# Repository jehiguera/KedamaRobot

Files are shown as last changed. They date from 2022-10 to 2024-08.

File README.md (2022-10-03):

# KedamaRobot
Autonomous Robot Kedama based on TM4C123G microcontroller

# The real Kedama cat


In this project, I have implemented a digital twin of my cat Kedama. The autonomous robot is based on a TM4C123G microcontroller namely TIVA C series TM4C123G by Texas instrumentals. 
The document [Autonomous Mobile robot Kedama.pdf] explains a detailed introduction of the architecture, requirements and firmware modules implemented using the IDE Keil MDK-ARM Plus version 5.
The microcontroller development board used for this project is TM4C123 Tiva C Series LaunchPad. 

https://github.com/jehiguera/KedamaRobot/blob/main/Autonomous%20Mobile%20Robot%20Kedama.pdf

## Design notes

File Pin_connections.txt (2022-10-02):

#define ECHO    (1U<<6)	// PB6(INPUT)
#define TRIGGER (1U<<4) // PA4 (OUTPUT)
#define BLUE_LED 1U<<2) //PF2 onboard Blue LED
#define IR_PIN  (1U<<5) //PA5 (INPUT)
#define SERVO   (1U<<3)	// PF3 (OUTPUT)
#define MOTOR1  (1U<<2)	// PE2 (OUTPUT)
#define MOTOR2  (1U<<3)	// PE3 (OUTPUT)

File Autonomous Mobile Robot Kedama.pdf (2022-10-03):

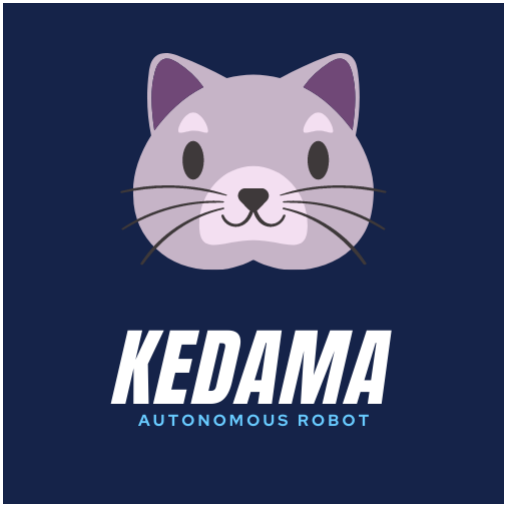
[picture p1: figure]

# Author: Jorge Higuera Portilla jhiguera@ieee.org Castelldefels, Barcelona, Spain. 15/05/2021

1

# The real Kedama cat

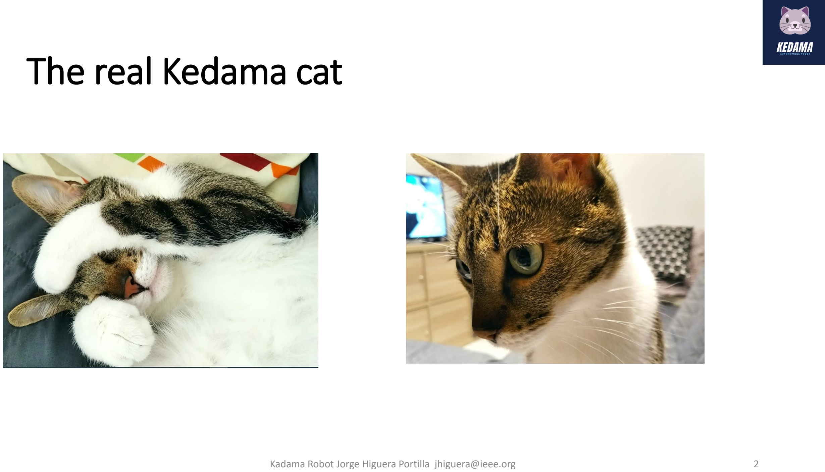
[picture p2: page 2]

Kadama Robot Jorge Higuera Portilla jhiguera@ieee.org | 2

# Kedama digital twin Robot Requirements

# Inputs and outputs

## Head: Ultrasonic sensor (Input / output)

## Intangible

## Neck: Servo Motor (output)

## Tail: IR sensor (Input)

## Limbs: DC motors (output)

## Tangible

## Timing: internal timers and HW interruptions

## Light: natural and artificial light detection

## Behavioral robot state: discovering, playing, shy

## Eco-location: ultrasonic wave

## Head: LEDs (output)

# Robot architecture

## Tail: IR sensor

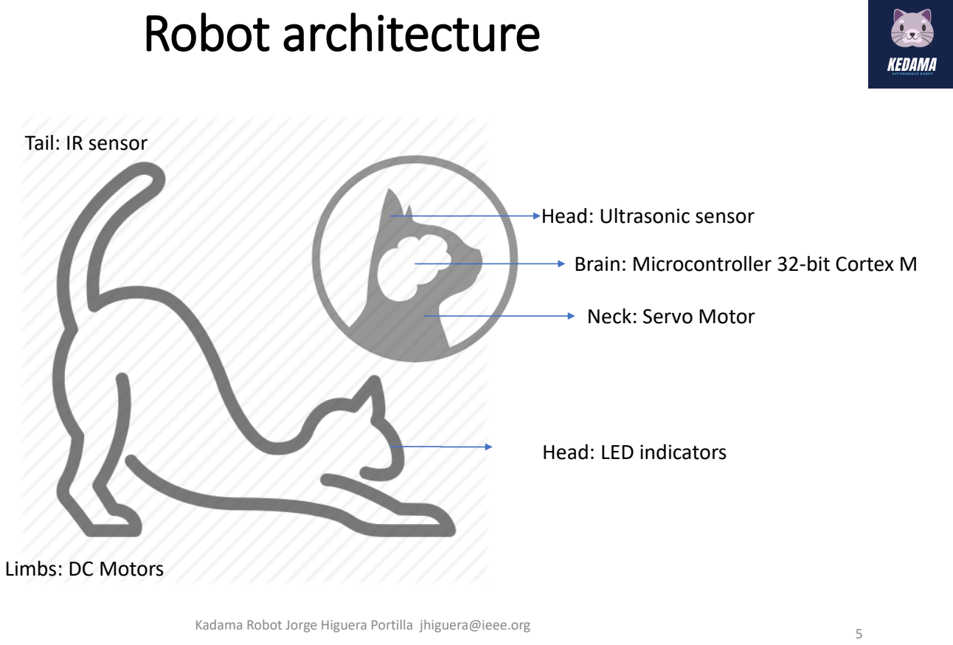
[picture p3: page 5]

## Brain: Microcontroller 32-bit Cortex M

## Head: Ultrasonic sensor

## Neck: Servo Motor

## Limbs: DC Motors

## Head: LED indicators

# Component and supplies

## (1 und) Tiva TM4C123G

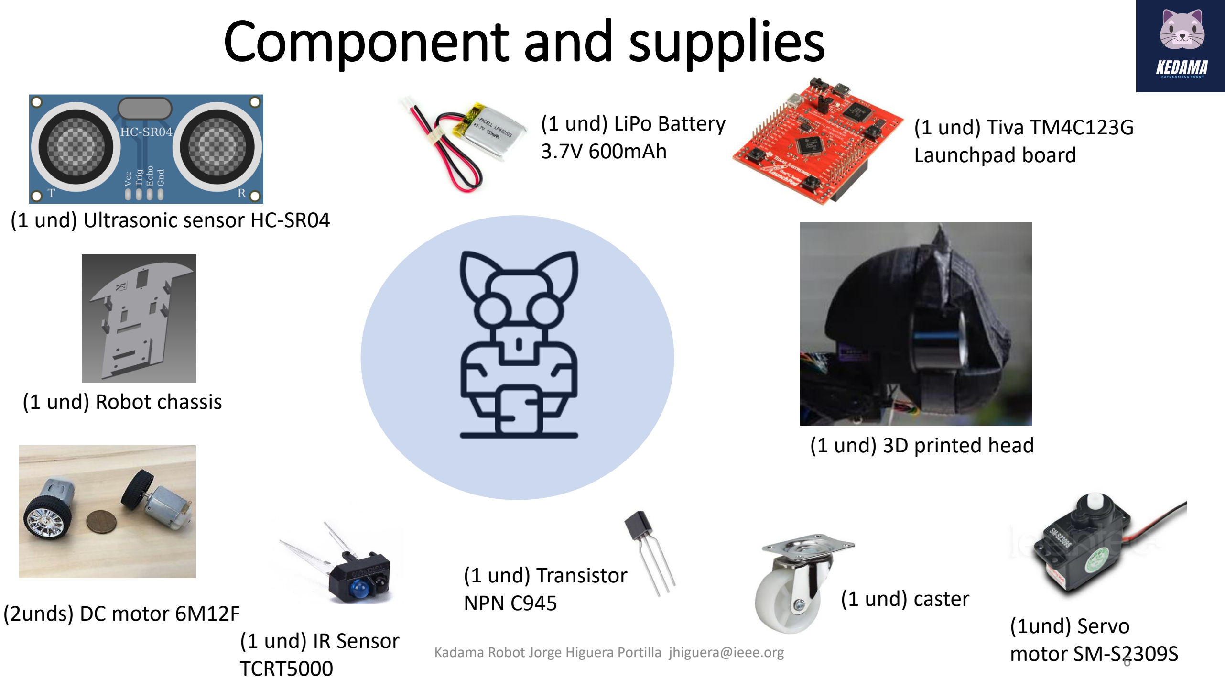
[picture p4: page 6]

## (1 und) Ultrasonic sensor HC-SR04

## Launchpad board

## (1 und) caster (2unds) DC motor 6M12F

## (1 und) 3D printed head

## (1 und) Robot chassis

## (1und) Servo motor SM-S2309S

## (1 und) Transistor NPN C945

## (1 und) IR Sensor TCRT5000

## (1 und) LiPo Battery 3.7V 600mAh

# Brain and Head configuration

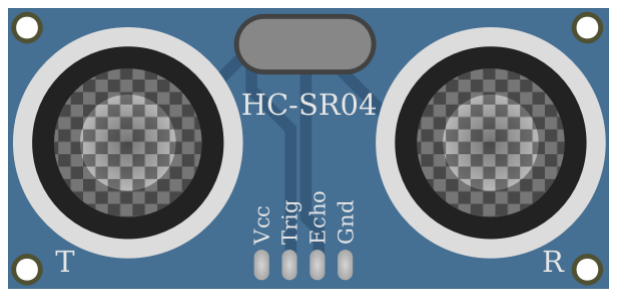
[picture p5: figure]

## Ultrasonic sensor HC-SR04

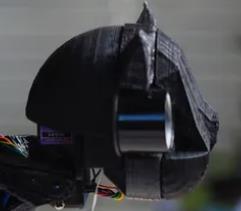
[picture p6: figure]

## 3D printed head

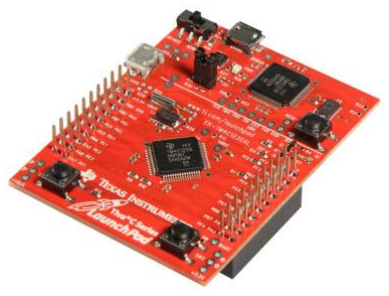
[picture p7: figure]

## Tiva TM4C123G Launchpad board with internal LEDs

# Tail configuration

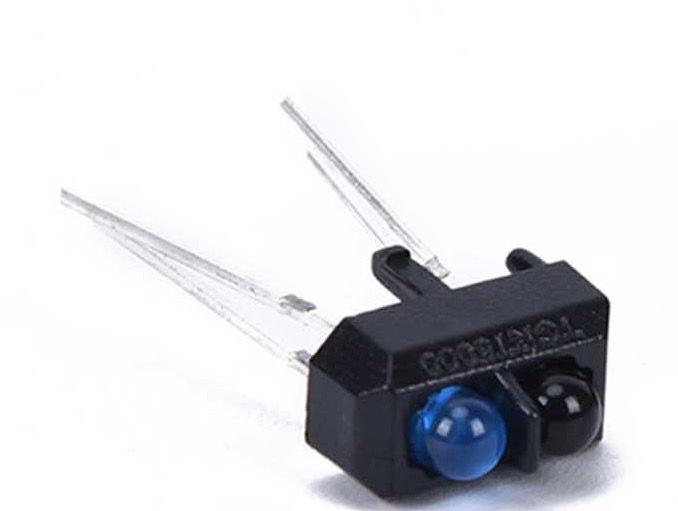
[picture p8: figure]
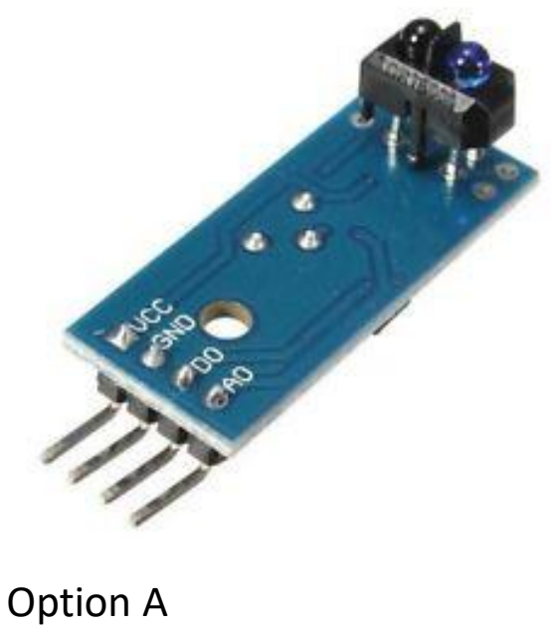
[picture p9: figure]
Option A

## IR Sensor TCRT5000

## Option B

# Limbs: wheels configuration

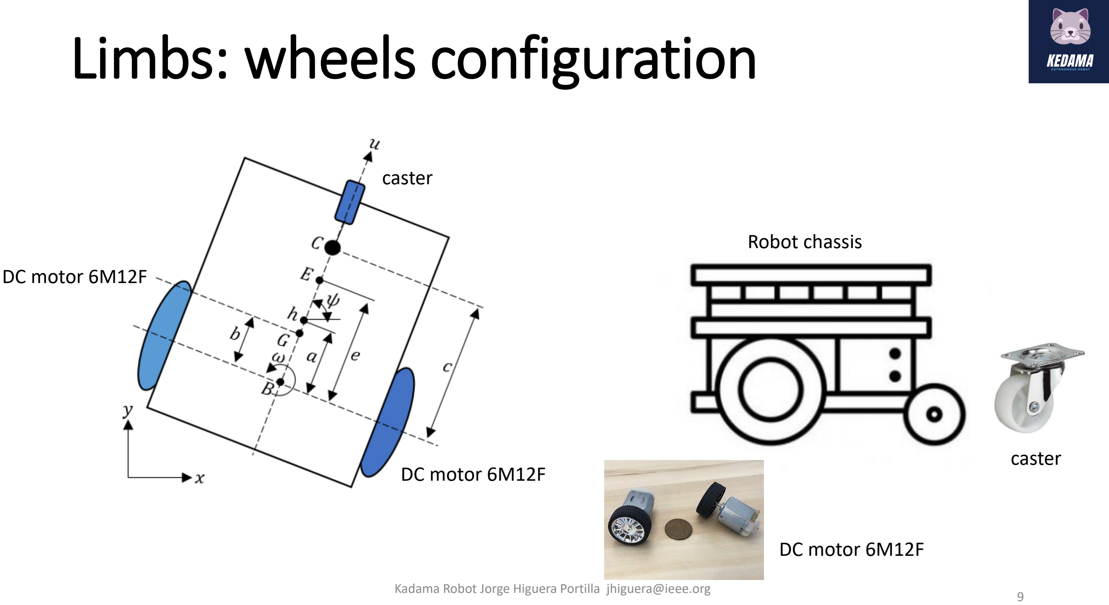
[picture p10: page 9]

## DC motor 6M12F

## caster

## Robot chassis

## DC motor 6M12F

## DC motor 6M12F

## caster

# 3D printing cat face

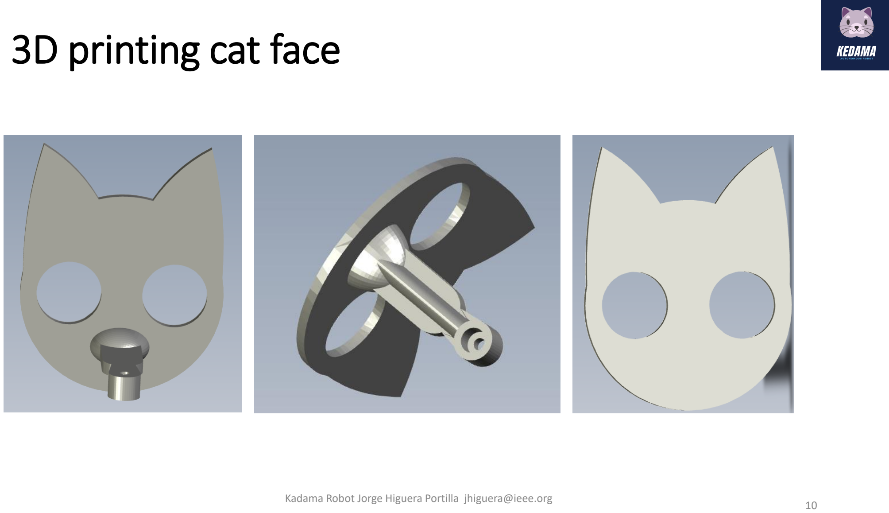
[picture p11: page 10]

# 3D printing robot chassis

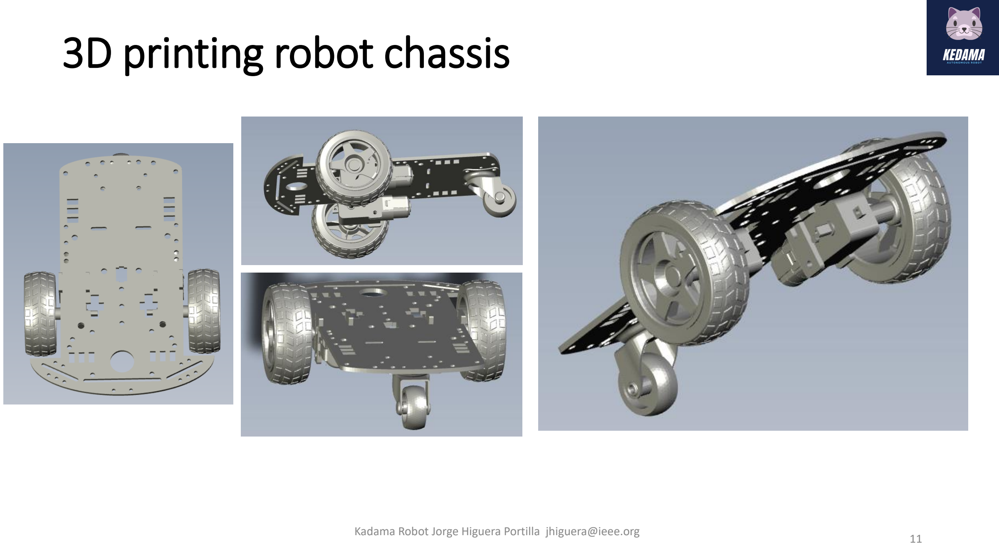
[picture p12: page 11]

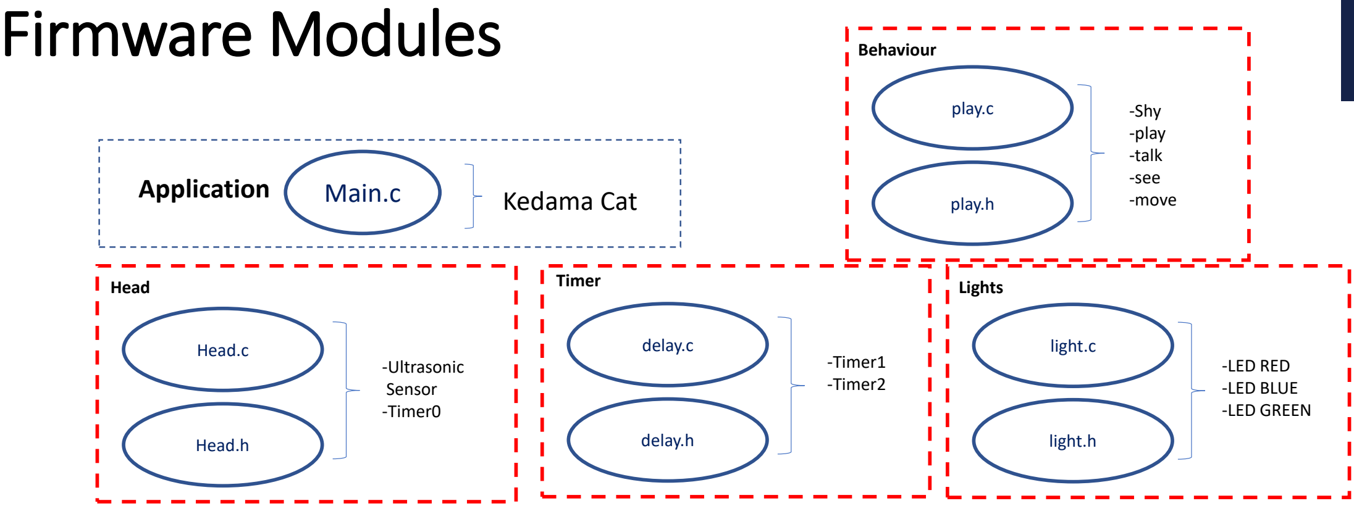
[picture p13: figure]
Firmware Modules; Main.c; Head.c; -Ultrasonic Sensor -Timer0; Kedama Cat Application; Head.h; Head; delay.c; -Timer1 -Timer2; delay.h; Timer; light.c; -LED RED -LED BLUE -LED GREEN; light.h; Lights; play.c; -Shy; -play -talk -see; play.h; -move; Behaviour
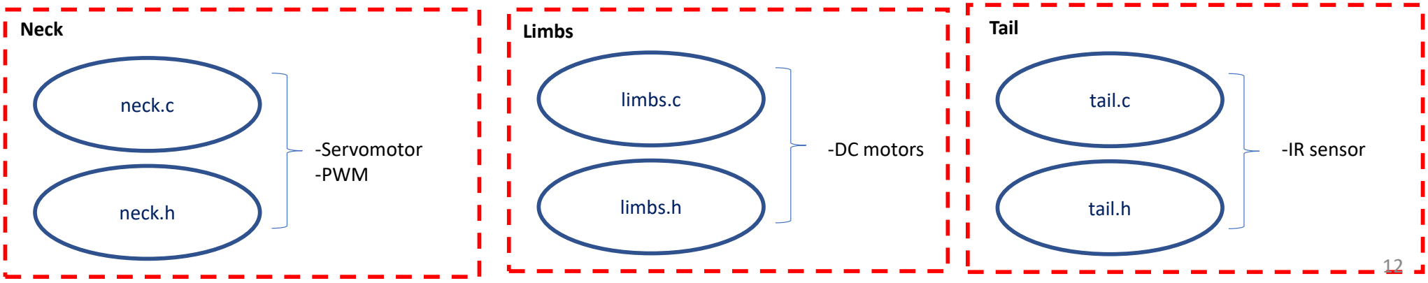
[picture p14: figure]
neck.c; -Servomotor -PWM; neck.h; Neck; limbs.c; -DC motors; limbs.h; Limbs; tail.c; -IR sensor; tail.h; Tail

Kadama Robot Jorge Higuera Portilla jhiguera@ieee.org

# Application Flowchart

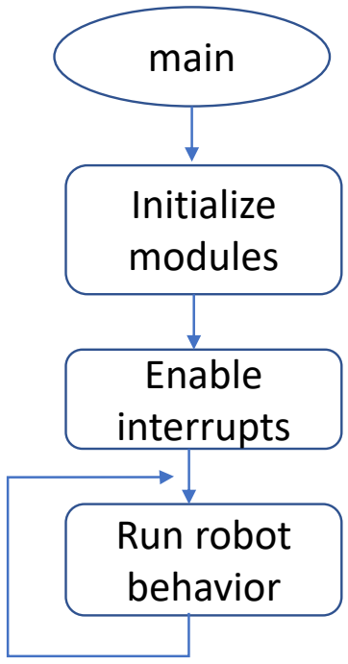
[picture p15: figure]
main; Initialize modules; Enable interrupts; Run robot behavior
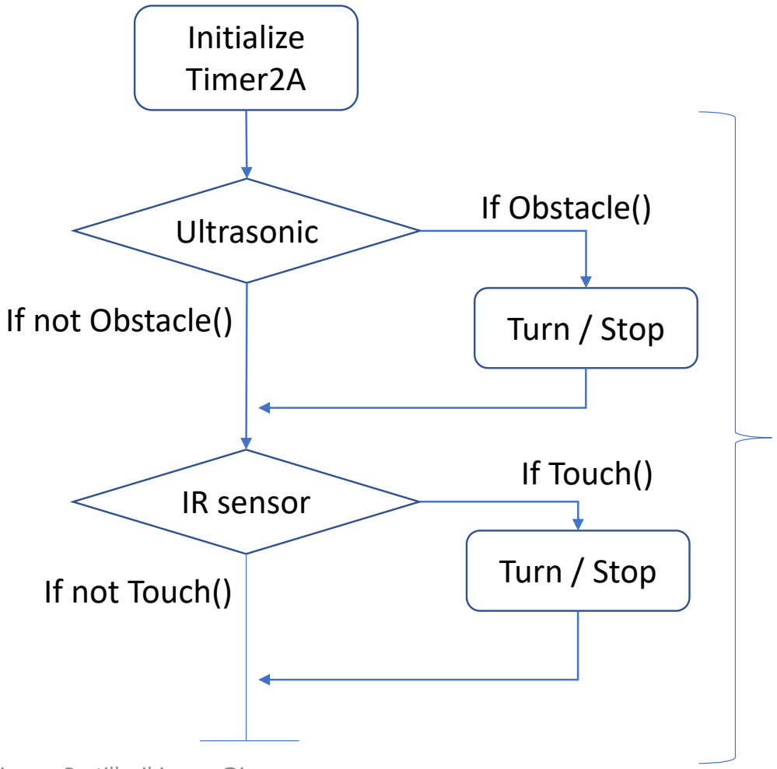
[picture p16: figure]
Initialize Timer2A; Ultrasonic; IR sensor; Turn / Stop; If Obstacle(); If Touch(); If not Obstacle(); If not Touch()

## Foreground thread Background thread

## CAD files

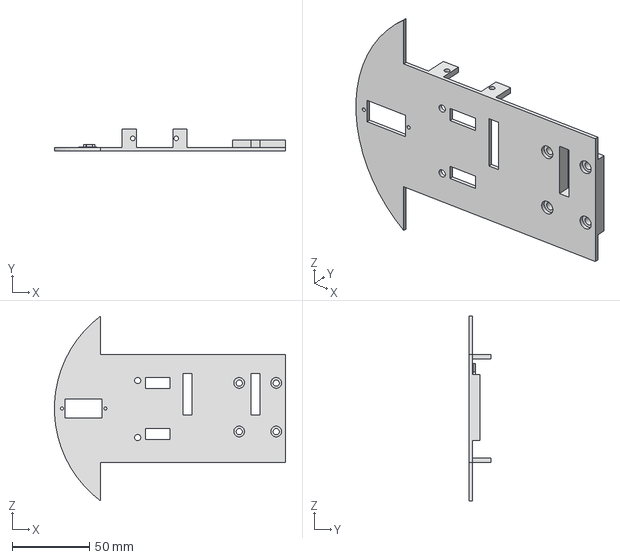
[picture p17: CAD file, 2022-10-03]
robot_chassis/chasis_robot_kedama_rev6.stp
149.9 x 14.0 x 120.0 mm

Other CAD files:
robot_chassis/chasis_robot_kedama_rev6.ipt
robot_chassis/chasis_robot_kedama_rev6.stl
robot_chassis/chasis_robot_kedama_rev7.ipt

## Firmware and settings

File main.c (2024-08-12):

/**@file: main.c
*	@author: Jorge Higuera
*	@email: jhiguera@ieee.org
*	@date: 12/08/2024
*	@brief: this file contaians functions to work with Kedama robot 
*/

//#include "TM4C123.h"
#include "TM4C123GH6PM.h"
#include "head.h"
#include "light.h"
#include "delay.h"
#include "neck.h"
#include "tail.h"
#include "limbs.h"
#include "play_around.h"

	uint32_t dist;
	
	
int main()
{
	//HEAD_Init();    /*initialization of ultrasonics sensor*/
	//LIGHTS_Init();  /*Initialization of RGB LEDS*/
	neck_init();    /*Initialization of servo motor*/
	//LIMBS_Init();   /*Initialization of DC motors*/
	//TAIL_Init();    /*Initialization of IR sensor.*/
	//timer2A_init(); /*Initialization of TIMER2A for interrupt */
	
	//echoAndTimer0_Init();
	
	//__enable_irq(); /* global enable IRQs */
	
	while(1)
	{
		//---------Test neck--------------
		//neck_move_right();
		//delay_Microsecond(1500000);
		//neck_move_center();
		//delay_Microsecond(1500000);
		//neck_move_left();
		//delay_Microsecond(1500000);
		//neck_move_center();
		neck_turn(1000);
		delay_Microsecond(15000000);
		neck_turn(160000);
		delay_Microsecond(15000000);
		neck_turn(319000);
		delay_Microsecond(15000000);
		neck_turn(160000);
		delay_Microsecond(15000000);
		//-----------------------------
		//delay_Microsecond(150000);
		//check_left();
		//delay_Microsecond(1500000);
		//check_right();
		//delay_Microsecond(1500000);
		//shy();   /** shy()	: Assigned robot behavior*/
    //play();
	}
	
}

// Background Thread

void TIMER2A_Handler(void)
{
	volatile int readback;
	if(TIMER2->MIS & 0x1)  //Timer2A timeout flag
	{
		//Thread content
		dist = headSensor_detect();
			
			if(dist<7)
			{
				GPIOF->DATA ^=(BLUE|RED|GREEN);
			}
			else
			{
				GPIOF->DATA =0x00;
			}
		
		TIMER2->ICR = 0x1; //Clear the timer2A timeout flag
		readback = TIMER2->ICR;
	}
	else
	{
		TIMER2->ICR = TIMER2->MIS; //Clear all flags
		readback = TIMER2->ICR; //a read to force clearing of interrupt flag
	}
}

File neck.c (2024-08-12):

/**@file neck.c
* @author J.Higuera
*	@email: jhiguera@ieee.org
*	@date: 12/08/2024
* @brief This file implements functions which initialize PWM control\n
*  for the servo motor.
*/

                   
#include "TM4C123GH6PM.h" // MCU package used
#include "delay.h"

#define LOAD_VALUE 320000 //Desired frequency= 50Hz  System frequency= 16MHz  Load value = 320000
#define MIN_DUTY_CYCLE 319000 //Value to rotate servo motor to the leftmost point
#define MAX_DUTY_CYCLE 1000 //Value to rotate servo motor to the rightmost point
#define _50P_DUTY_CYCLE 160000 //Value to rotate servo motor to the mid-point


void neck_init(void)
{
	int i = 0;
	//Enable peripheral clocks
	SYSCTL->RCGCPWM |= 2; //Enable clock to PWM1 
	SYSCTL->RCGCGPIO |= 0x20; //Enable clock to PORTF
	SYSCTL->RCC &= ~0x00100000; // No pre-divide for PWM clock
		while(i<40){i++;}
		
		//Enable port PF3 for PWM1 M1PWM7
		GPIOF->AFSEL = 8; //(1000) PF3 uses alternative function
		GPIOF->PCTL &= ~0x0000F000; //make PF3 PWM output pin step A
		GPIOF->PCTL |= 0x00005000; //Step B
		GPIOF->DEN |= 8; //pin digital enable
	
		PWM1->_3_CTL =0;//disable the PWM before configuration stop counter
		PWM1->_3_GENB =0x0000008C; //M1PWM7 output set when reload
		PWM1->_3_LOAD = LOAD_VALUE-1;//LOAD_VALUE = (1/Desired PWM frequency)*System frequency
		PWM1->_3_CMPA = MIN_DUTY_CYCLE; //set duty cycle %
		PWM1->_3_CTL = 1; //start timer
		PWM1->ENABLE = 0x80; //start PWM1 CH7
}

void neck_turn(uint32_t amount)
{
	PWM1->_3_CMPA = amount;
}

void check_left(void)
{
	uint32_t i;
	
	PWM1->ENABLE |= 0x80;
	for(i=319000; i<=1; i-=5000)
	{
		PWM1->_3_CMPA = i;
		delay_Microsecond(500000); //1 seg
	}
	PWM1->ENABLE &= ~0x80;
}

void check_right(void)
{
	uint32_t i;
	
	PWM1->ENABLE |= 0x80;
	for(i=1000; i<=160000; i+=1000)
	{
		PWM1->_3_CMPA = i;
		delay_Microsecond(100000); //1seg
	}
	PWM1->ENABLE &= ~0x80;
}

void neck_move_left(void)
{
	PWM1->_3_CMPA = MIN_DUTY_CYCLE;
}

void neck_move_right(void)
{
	//PWM1->ENABLE |= 0x80;
	PWM1->_3_CMPA = MAX_DUTY_CYCLE;
	//PWM1->ENABLE &= ~0x80;
}

void neck_move_center(void)
{
	PWM1->_3_CMPA = _50P_DUTY_CYCLE;
}
